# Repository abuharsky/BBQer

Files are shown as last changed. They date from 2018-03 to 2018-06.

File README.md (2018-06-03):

> This is the first, alpha version of documentation. It will be improved. I'll waiting for your questions

# BBQer
Hello, my name is Alex, I'm from Russia and I love BBQ!
So, BBQ Smokers are not so popular in Russia, thats why I'am the only one in my small town - therefore the best :) !

There are a lot of different handmade of factorymade BBQ Smoker temperature controllers, but for me all of them have too many limitations.
For example, for assembling very popular "HeaterMeter" you need to be an good engineer with soldering skills.
Or, you need to spent a lot of time to assemble, debug and configure some other DIY projects.
Or it cost too much!

As for me, this is not an easy way.

I hope, that I can explain to you, how to get very easy, cheap, really, extra-cheap controller with an optional cloud monitoring, that perfectly solve every BBQSmoking needs!

### Let's begin!

What's is the main problem for Low&Slow smoking?! Right, it takes too many hours! You need to constantly maintain temperature level and smoke density.

For maintaining constant temperature you need to always change an airflow using damper.

Airflow provide the main heat and smoke transfer from burning wood and charcoals to the meat.

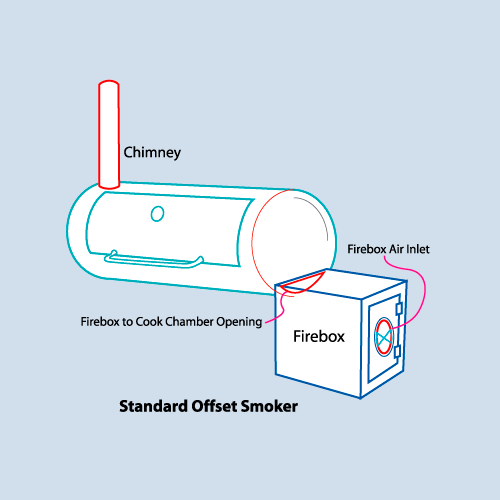
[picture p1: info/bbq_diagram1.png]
standart offset smoker


So, we need only to add a simple temperature sensor and electronically controlled air blower/damper.
Controller periodically reads temperature and adjust the airflow.

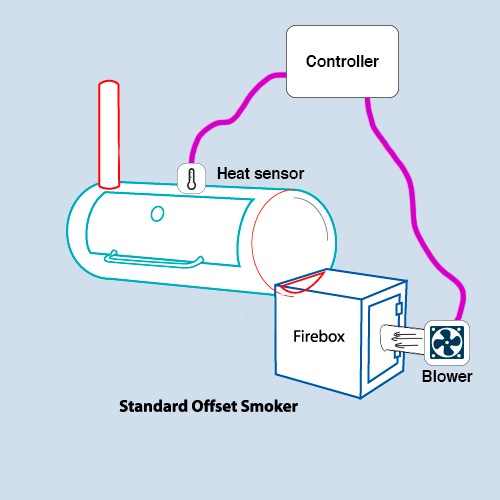
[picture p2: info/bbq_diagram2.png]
standart offset smoker with temperature controller


That's how does it must work.

### Part 1. Arduino based controller

### Hardware

As I say before, I don't think that we need to be an engineer with soldering skills! You don't need to solder anything (maybe exept few connectors).

You need to buy:

1x [arduino nano (~3$)](https://ru.aliexpress.com/store/product/Arduino-Nano-3-0-Arduino-Nano-CH340-usb/1602024_32841140539.html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)

1x [arduino nano I/O extension board(~1$)](https://ru.aliexpress.com/item/1Pcs-I2C-NANO-I-O-Expansion-Sensor-Shield-Module-For-Arduino-UNO-R3-Nano-V3-0/32829846130.html)

1x [temperature sensor (K-type thermocouple with required amplifier)(~3$)](https://ru.aliexpress.com/item/MAX6675-Module-K-Type-Thermocouple-Temperature-Sensor/32698965438.html)

1x [blower fan(~2.5$)](https://ru.aliexpress.com/item/Brushless-DC-Blower-Cooling-Fan-Sleeve-Bearing-7525S-12V-0-18A-75x33mm-75mm/32731387269.html)

1x [mosfet driver(~0.5$)](https://ru.aliexpress.com/item/TOP-MOSFET-Button-IRF520-MOSFET-Driver-Module-ARM-Raspberry-pi/32662485350.html)

1x [wires (~3$)](https://ru.aliexpress.com/item/Dupont-Wire-Male-to-Male-Male-to-Female-Female-to-Female-Jumper-Cable-120x10cm/32729974130.html)

1x [power converter (~1$)](https://ru.aliexpress.com/item/XL6009-DC-Adjustable-Step-up-boost-Power-Converter-Module-Replace-LM2577/32636472543.html)

##### Total: ~14$ (without delivery)
(I recommend to use same supplier for faster delivery)

Also, you can optionally purchase:

1x [servo (~3$)](https://ru.aliexpress.com/item/MG90S-Micro-Servo-RC/32843925047.html?spm=a2g0s.9042311.0.0.jh7MDU) for more fine aiflow control

1x [thermo probe (~7$)](https://ru.aliexpress.com/item/Thermopro-Thermometer-extra-probe/32778050836.html?spm=a2g0s.9042311.0.0.jh7MDU) for food(meat) temperature control. You can connect up to 8 probes.

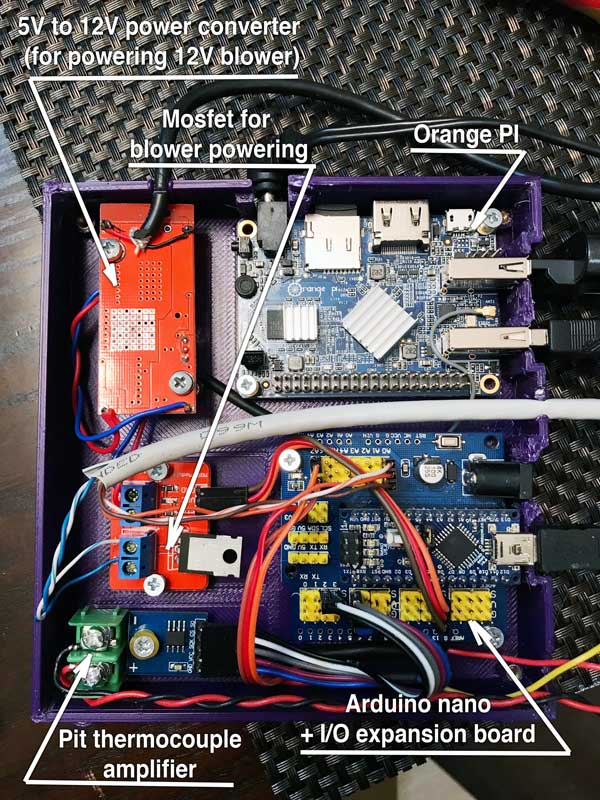
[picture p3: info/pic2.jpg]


# BEFORE ASSEMBLING!!!

Don't connect your motor to power converter.
First you need to adjust output voltage to 12V.
Using multimeter adjust voltage regulator on the blue box.

### Software

first, you need to add to your arduino *[SerialCommand](https://github.com/kroimon/Arduino-SerialCommand)* library

next, flash an arduino using this **repository/arduino/BBQController/**

next, open serial monitor (baud 115200) and type any of commands below:

* **target** <temp> - set target temp to specified value, this command start temperature controller, example: "target 110" - set the target temp to 110С or "target 0" - disables temperature controller

optional, manual managment commands:

* **temp** - print current temp from all sensors
* **servo** <angle> - move servo to specified angle
* **damper** <position> - open or close damper, position value between 0.0(closed) and 1.0(fully opened)
* **motor** <power> - powers the blower, power value between 0.0(disabled) and 1.0(full power)

This is enougth! You can setup your arduino controller, all values will be stored in EEPROM(energy independent memory). So, set the target temp to 110C (for brisket) and use great and cheap temperature controller.

I think, that we don't need to setup an additional display for arduino controller (Maybe I'll change my opinion in the future).
If you need display or some kind of user interface to this arduino controller, let's go to part 2!

### Part 2. Orange PI + cloud monitoring

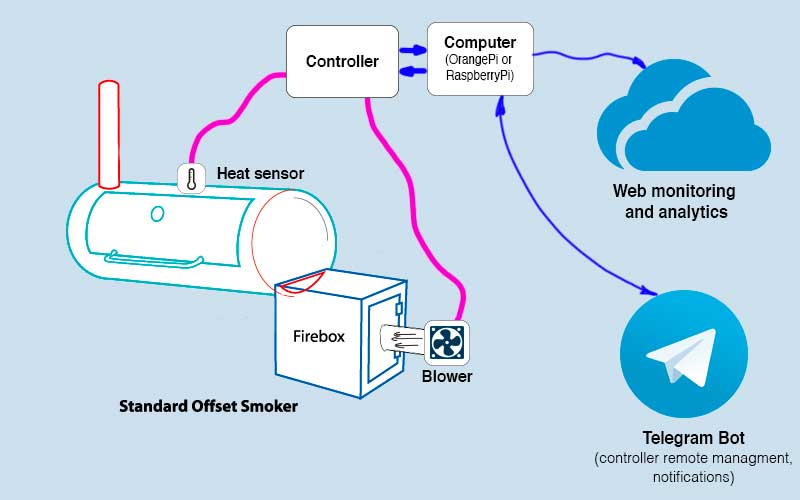
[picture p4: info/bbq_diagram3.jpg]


### Hardware

I recommend to use an orange pi lite (~12$).

### Software

As I say before, I don't want to setup direct display with some buttons on arduino. Because everyone already have display!
We will use your phones and tablets! And, of course, internet!

So, after you setup your PI (you can use one of thousands instructions from internet), you need to setup python3 and required packages, just type in the pi terminal the commands below:

> apt-get install python3
> 
> apt-get install python3-pip
> 
> pip3 install requests
> 
> pip3 install telebot
> 
> pip3 install pyserial

After installing, copy 
BBQer/cloudClient/bbqcontroller.py

BBQer/cloudClient/configuration_empty.txt

to your pi home dir, then, **rename configuration_empty.txt** to **configuration.txt** and fill required parameters

We will use telegram bot for sending commands to controller and receive information.

### Cloud monitoring

I recommend to use **corlysis.com** , free account is enough for our temperature monitoring.

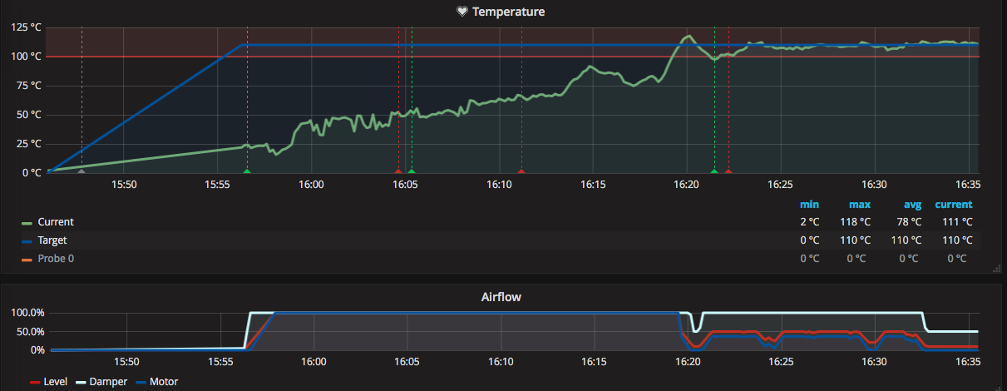
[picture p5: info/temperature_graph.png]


Setup database, than copy required db name and token to **configuration.txt**, than open grafana and import dashboard from **grafana.json**

Now, you can use your mobile phone to control your BBQ, view temperature graphs and receive notifications!

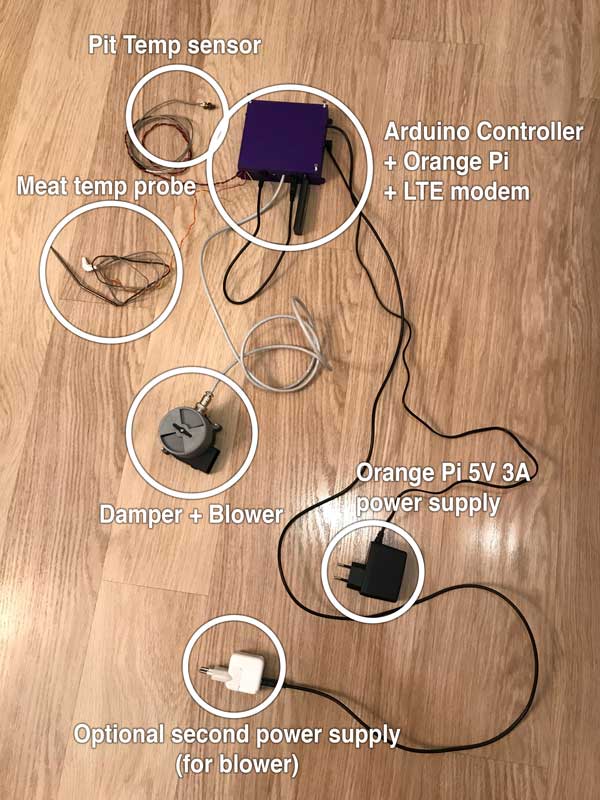
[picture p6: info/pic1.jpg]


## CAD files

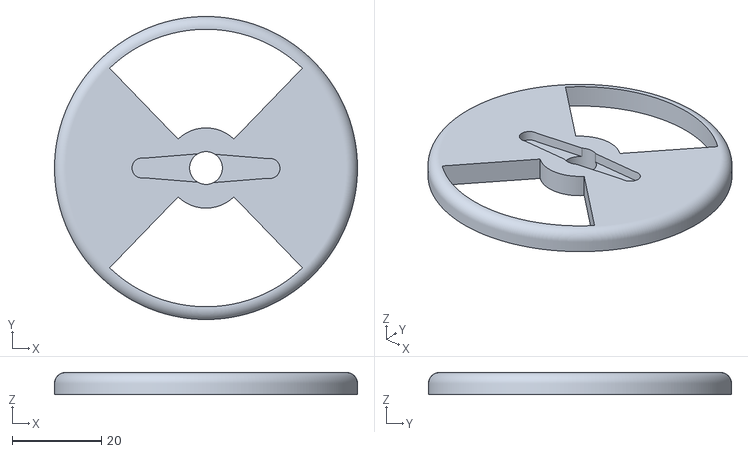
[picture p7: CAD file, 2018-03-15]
3dprint/damper_top.stl
68.0 x 68.0 x 5.00

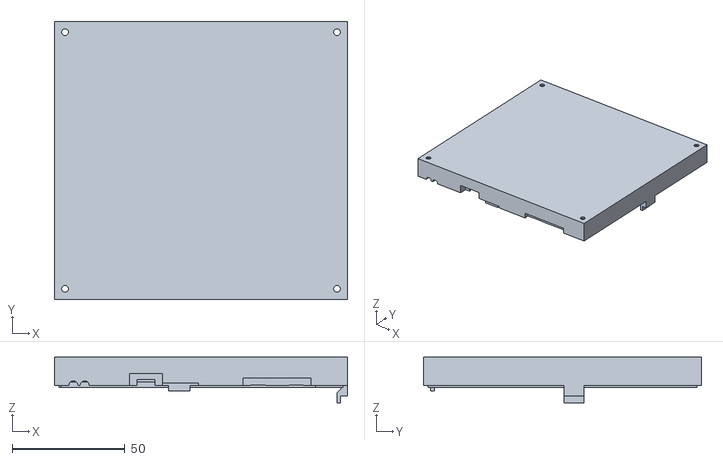
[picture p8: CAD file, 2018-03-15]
3dprint/electronics_box_top.stl
130.0 x 123.2 x 20.2

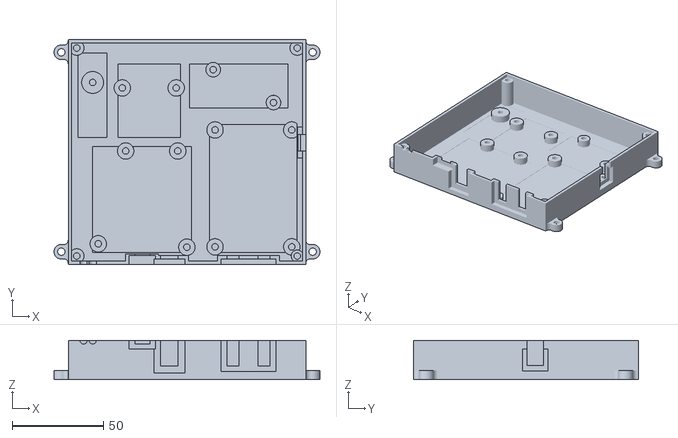
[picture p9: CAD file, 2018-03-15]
3dprint/electronics_box_bottom.stl
145.6 x 123.2 x 21.5

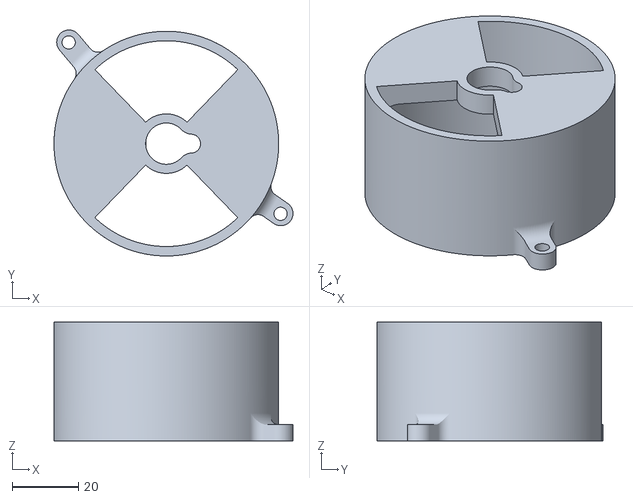
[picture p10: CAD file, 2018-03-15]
3dprint/damper_bottom.stl
72.3 x 68.4 x 36.0

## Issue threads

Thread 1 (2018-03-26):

Schematic needed

TorokBalazs75, 2018-03-26:
hello abuharsky, I love BBQing just like you probably, so I was glad reading your comment on arduino project hub, but honestly I'm a real beginner building a controller like this. Is it possible to have a schematic  for the electronics? Next will be the programming, but I hope I will help with that one :) thanks a lot, Balázs

abuharsky, 2018-03-27:
Ok, no problem I will add schematic very very soon

TorokBalazs75, 2018-03-27:
👍

TorokBalazs75, 2018-04-25:
hi there, schematic is more professional, but even if you could pull apart the boards little bit to see the wiring better would be helpful, thanks&regards, Balázs

abuharsky, 2018-05-23:
Im sorry for long answer, I tried some schematic tools, but they dont have a lot of used components, so, I can make a video

TorokBalazs75, 2018-05-23:
actually - as I'm still learning - found that it is pretty much well defined in the source code, but a video might be helpful

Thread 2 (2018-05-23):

max6675 error

TorokBalazs75, 2018-05-23:
hi Abuharsky, finaly I got my parts and started to work on the project, but unfortunately ran into an issue already. When I try to upload the controlling program to arduino, it fails with missing source-code for max6675, could you please advise? thanks a lot

abuharsky, 2018-05-23:
ooh, no problem, just download this one

https://github.com/adafruit/MAX6675-library

and put it to your arduino library folder or use this instruction

https://www.arduino.cc/en/Guide/Libraries#toc5

abuharsky, 2018-05-23:
no problem

TorokBalazs75, 2018-05-23:
hi, so I successfully loaded code on arduino, connected everything together. Now I can communicate with arduino, thermocouple reads temp. However damper open/closes on command, if current temp is 23 and I set target to 30, I would expect damper close and ventillator turn off when reaching target temp, but it doesn't happen so:

[BBQctrler_1st_use.txt](https://github.com/abuharsky/BBQer/files/2032538/BBQctrler_1st_use.txt)

also, at first, I used a 5V blower attached to the mosfet, then I wanted to try the 12V blower through the booster  connected to mosfet, but only gave clicking noise, then I put back the 5V blower to mosfet, but it doesn't work, so I'm afraid, that something happend to the mosfet :(

abuharsky, 2018-05-23:
make a photo of assembled electronics

TorokBalazs75, 2018-05-23:
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

abuharsky, 2018-05-23:
contact me on fb https://www.facebook.com/abuharsky

jzGitHub-01, 2020-01-13:
Hi abuharsky,
Can I ask you some question which realted to bbq topic?
Maybe on FB?

MTBrewer, 2020-06-17:
Did you ever figure out your damper and what was causing the clicking noise in the blower?

abuharsky, 2020-06-20:
Noise is ok, you hear it because of PWM signal.

stunt77, 2020-08-04:
Hi, same problem blower stopped with noise, how i can solve tks

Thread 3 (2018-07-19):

Grill Open Logic

paintflinger, 2018-07-19:
Trying to teach myself the programming language to potentially incorporate myself, but have you considered adding programming logic for when you open up the grill?

For example, if the Grill Temperature decreases at a rate greater than 2 degrees / second then the temperature controller will exit the control loop for a set period (e.g. 5 minutes) to allow the grill to achieve steady state again.

abuharsky, 2018-07-23:
Maybe Grill Door open/close sensor needed. I will make some experiments.

Thank you for idea.

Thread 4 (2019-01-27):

Schematic

ghojezz, 2019-01-27:
Hello there,

I'm really new to this kind of thing and I don't have any background in tinkering with electronics, arduino, etc but I'm willing to learn. Can you draw us a diagram using Fritzing application if you don't mind?

abuharsky, 2019-01-27:
Hey!

I working for a new version, that twice as cheaper and twice as easier to assemble. But with the same level of functionality!

I dont want to work more about this old version, so, I will describe deeply new version to help ypu to assemble it.

I you want, I can say you part numbers of new components.
While you will wait for delivery, I will make some new wiki articles.

mhnudi, 2019-07-16:
Hello! I was just reading through some of your comments and found this one saying you might be working on a newer version. I was just wondering if this was still the case? I am hoping to perform a similar modification like you have but if you are in the process of working on a simpler version I would definitely be interested. Thanks!

alambert-irl, 2020-04-20:
Hi @abuharsky.

Alex here, just been looking at building your project. I can see from your photos that you have a damper and fan combined. Do you have a link for the damper you used, are you using this [servo](https://aliexpress.ru/item/32843925047.html?spm=a2g0s.9042311.0.0.jh7MDU)to control the damper?

Thanks - Alex trying to survive quarantine in Ireland

abuharsky, 2020-04-29:
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

Hi, sorry for late answer, yea, servo is ok

jlsegb, 2020-06-26:
In case anyone is struggling like my friends and I were. Here are more pictures with a little more detail.
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

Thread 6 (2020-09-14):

Cloud / Telegram issue?

balazsraacz, 2020-09-14:
Hi Alexander,

not sure if this project is still open or used by anyone. Despite all my efforts I can't get the communication with telegram working and getting errors with the python file as well.

 "python3 bbqcontroller.py"
I get the following error:
"root@orangepilite:~/BBQer/cloudClient# python3 bbqcontroller.py
Traceback (most recent call last):
  File "bbqcontroller.py", line 10, in <module>
    config.read('/root/BBQer/cloudClient/configuration.txt')
  File "/usr/lib/python3.5/configparser.py", line 696, in read
    self._read(fp, filename)
  File "/usr/lib/python3.5/configparser.py", line 1077, in _read
    raise MissingSectionHeaderError(fpname, lineno, line)
configparser.MissingSectionHeaderError: File contains no section headers.
file: '/root/BBQer/cloudClient/configuration.txt', line: 1
'\ufeff[arduino]\n'
"

Either way appreciate the help

balazsraacz, 2020-10-18:
The solution to run the script seems to have been the config file it pulled in was in the root rather than the correct in home.

Closed 2020-10-18.

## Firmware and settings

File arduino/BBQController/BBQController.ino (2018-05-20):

#include <SerialCommand.h>
#include "max6675.h"
#include <Servo.h>
#include "DCMotor.h"
#include "SmoothServo.h"
#include "Damper.h"
#include "ThermoProbe.h"
#include "TemperatureController.h"

#define SERVO_PIN A0
#define SERVO_MIN_ANGLE 0
#define SERVO_MAX_ANGLE 90

#define MOTOR_PIN 11

#define PROBE0_PIN A4
#define PROBE1_PIN A7

#define THERMO_S0  2
#define THERMO_CS  3
#define THERMO_CLK 4


Servo servo;
SmoothServo smoothServo(servo, SERVO_PIN);
DCMotor motor(MOTOR_PIN);
Damper damper(smoothServo, SERVO_MIN_ANGLE, SERVO_MAX_ANGLE);
MAX6675 thermocouple(THERMO_CLK, THERMO_CS, THERMO_S0);
ThermoProbe probe0(PROBE0_PIN, 200000, 4220);
ThermoProbe probe1(PROBE1_PIN, 200000, 4220);

TemperatureController controller(damper, motor, thermocouple, probe0, probe1);

SerialCommand sCmd;

void setup()
{
  Serial.begin(115200);

  motor.setup();
  controller.setup();
  probe0.setup();
  probe1.setup();

  // Setup callbacks for SerialCommand commands
  sCmd.addCommand("servo", servoControl);
  sCmd.addCommand("damper", damperControl);
  sCmd.addCommand("motor", motorControl);
  sCmd.addCommand("temp", getTemperature);
  sCmd.addCommand("target", setTargetTemperature);
  sCmd.addCommand("controller", setControllerParameters);
  sCmd.setDefaultHandler(unrecognized);

  Serial.println("Ready");
}

void loop()
{
  motor.loop();
  controller.loop();
  probe0.loop();
  probe1.loop();
  sCmd.readSerial();
}

//---------------------------------------------

void servoControl() {
  char *arg;

  arg = sCmd.next();
  if (arg != NULL) {
    smoothServo.setAngle(atoi(arg)); 
    smoothServo.printState();
  }


}

void damperControl() {
  char *arg;

  arg = sCmd.next();
  if (arg != NULL) {
    damper.setPosition(atof(arg)); 
    damper.printState();
 }


}

void motorControl() {
  char *arg;

  arg = sCmd.next();
  if (arg != NULL) {
    motor.setPower(atof(arg));
    motor.printState();
  }

}

void setTargetTemperature() {
  char *arg;

  arg = sCmd.next();
  if (arg != NULL) {
    controller.setTargetTemperature(atof(arg));
  }

  arg = sCmd.next();
  if (arg != NULL) {
    controller.setPrintStateInterval(atof(arg)*1000);
  }
}

void setControllerParameters() {
  char *printInterval   = sCmd.next();
  char *airFlowMin      = sCmd.next();
  char *airFlowMax      = sCmd.next();
  char *airFlowStepUp   = sCmd.next();
  char *airFlowStepDown = sCmd.next();
  
  if (printInterval != NULL && 
      airFlowMin != NULL && airFlowMax != NULL && 
      airFlowStepUp != NULL && airFlowStepDown != NULL) 
  {
    controller.setPrintStateInterval(atof(printInterval)*1000);
    controller.setAirflowLimitsAfterTempReached(atof(airFlowMin), atof(airFlowMax));
    controller.setAirflowChangeSteps(atof(airFlowStepUp), atof(airFlowStepDown));

    controller.printParameters();
  }
  else {
    Serial.println("Wrong 'controller' command arguments, must be:");
    Serial.println("> controller printInterval(seconds) airFlowMinWhenTempReached(float) airFlowMaxWhenTempReached(float) airFlowStepUp(float) airFlowStepDown(float)");
    Serial.println("Example:");
    Serial.println("> controller 10 0.3 0.7 0.05 0.15");
  }

}

void getTemperature() {
  Serial.print("[TEMP] PIT=");
  Serial.print(thermocouple.readCelsius());
  Serial.print("C, PROBE1=");
  Serial.print(probe0.readCelsius());
  Serial.print("C, PROBE2=");
  Serial.print(probe1.readCelsius());
  Serial.print("C");
  Serial.println();
}

void unrecognized(const char *command) {
  Serial.println("Unrecognized command");
}

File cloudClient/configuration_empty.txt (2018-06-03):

[arduino]
port=/dev/ttyUSB0
baud=115200

[telegram]
chatId=111222
botToken=511122334455:XXXXXXXXX-XXXXXXXXX-XXXXXXXXX
proxyType=
proxyAddress=

[corlysis]
db=BBQControl
token=XXXXXXXXXXXXXXXXXXXXXXXXXXX

[system]
runCommandOnNoInternet=sudo ifconfig wlan0 down && sleep 5 && sudo ifconfig wlan0 up && exit 0

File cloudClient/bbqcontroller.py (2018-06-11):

#!/usr/bin/python
import serial, time, threading, json, datetime, requests, configparser, os, queue, logging
#-------------------------
# config
#-------------------------

config = configparser.ConfigParser()
config.read('/root/BBQer/cloudClient/configuration.txt')

usbDevice = config.get('arduino', 'port')
usbSpeed  = config.get('arduino', 'baud')

chatId       = config.get('telegram', 'chatId')
botToken     = config.get('telegram', 'botToken')
proxyType    = config.get('telegram', 'proxyType')
proxyAddress = config.get('telegram', 'proxyAddress')

proxy = {}
if proxyType and proxyAddress:
	proxy = {proxyType:proxyAddress}

dbName    = config.get('corlysis', 'db')
dbToken   = config.get('corlysis', 'token')

networkLostCommand = config.get('system', 'runCommandOnNoInternet')
networkRestartRetriesBeforeRestart = 0
networkRestartMaxRetries = 5
networkErrorsCounter = 0 #count every send operation error
networkMaxErrorCount = 5

#---------
serial_port = serial.Serial(usbDevice, usbSpeed)

main_thread_queue = queue.Queue()
network_thread_queue = queue.Queue()

logging.basicConfig(filename="/root/BBQer/cloudClient/logs/bbqcontroller"+str(time.time())+".log", level=logging.INFO)


def run_on_main_thread(function):
	main_thread_queue.put(function)

def run_on_network_thread(function):
	network_thread_queue.put(function)

#-------------------------
# corlysis
#-------------------------

def plot_json(data):
	obj = json.loads(data)

	# currenttime = '{0:%H:%M:%S}'.format(datetime.datetime.now())

	airflow  = obj["airflow"]["level"]
	damper   = obj["airflow"]["damper"]
	motor    = obj["airflow"]["motor"]
	curtemp  = obj["temperature"]["current"]
	probe0   = obj["temperature"]["probe0"]
	probe1   = obj["temperature"]["probe1"]
	target   = obj["temperature"]["target"]

	url = 'https://corlysis.com:8086/write'
	
	params = {"db": dbName, "u": "token", "p": dbToken}
	
	payload = "temperature_data current="+curtemp+",target="+target+",probe0="+probe0+",probe1="+probe1+"\nairflow_data level="+airflow+",damper="+damper+",motor="+motor+"\n"
	
	global networkErrorsCounter
	try:
		resp = requests.post(url, params=params, data=payload, timeout=10)
		resp.raise_for_status()
	except Exception as err:
		networkErrorsCounter += 1
		logging.info('Error sending plot data: ' + str(err))
		print('Error sending plot data: ' + str(err) + '\n' + payload)


#-------------------------
# serial
#-------------------------

def write_line_to_serial_port(line):
	logging.info('[serial] <- ' + line)
	print('[serial] <- ' + line)
	serial_port.write(line.encode())
	serial_port.write(b'\n')

def handle_serial_port_data(data):
	logging.info('[serial] -> ' + data)
	print('[serial] -> ' + data)
	
	# detect json data
	if (data.startswith( '{' )):
		run_on_network_thread(lambda: plot_json(data))
	else:
		run_on_network_thread(lambda: telegram_send_message(chatId, 'serial: '+data))

def read_from_serial_port(serial_port):
	while True:
		line = serial_port.readline().decode()
		run_on_main_thread(lambda: handle_serial_port_data(line))
		time.sleep(1)

thread_serial_port = threading.Thread(target=read_from_serial_port, args=(serial_port,))
thread_serial_port.start()


#-------------------------
# telegram bot
#-------------------------

def telegram_send_message(to, text):
	global networkErrorsCounter
	try:
		resp = requests.get('https://api.telegram.org/bot' + botToken + '/sendMessage?chat_id=' + to + '&text=' + text, proxies=proxy, timeout=10)
		resp.raise_for_status()
	except Exception as err:
		networkErrorsCounter += 1
		logging.info('Error sending message to telegram ' + str(err))
		print('Error sending message to telegram ' + str(err))

def telegram_get_updates():
	offset = 0
	while True:
		try:
			resp = requests.get('https://api.telegram.org/bot' + botToken + '/getUpdates?timeout=30&allowed_updates=["message"]&offset=' + str(offset), proxies=proxy, timeout=30)
			if resp.status_code == 200:
				offset = process_telegram_updates_response(resp.json())
			else:
				resp.raise_for_status()
		except requests.exceptions.Timeout:
			time.sleep(3) #no updates, run next iteration
			continue
		except Exception as err:
			logging.info('telegram "getUpdates" error: ' + str(err))
			print('telegram "getUpdates" error: ' + str(err))
			time.sleep(15)
			continue
		time.sleep(1)

def process_telegram_updates_response(json):
	offset = 0
	updates = json["result"]
	for index, update in enumerate(updates):
		run_on_main_thread(lambda: process_telegram_message(update["message"]))
		offset = int(update["update_id"])
	return offset + 1

def process_telegram_message(message_json):
	if chatId == str(message_json["from"]["id"]): 
		text = message_json["text"]
		logging.info('[telegram] ' + text)
		print('[telegram] ' + text)
		if text.startswith('/cputemp'):
			file = open("/etc/armbianmonitor/datasources/soctemp", "r")
			run_on_network_thread(lambda: telegram_send_message(chatId, "CPU temp:{:.1f}C".format(float(file.read())/1000)))  
		elif text.startswith('/serial'):
			run_on_main_thread(lambda: write_line_to_serial_port(text[8:]))
		elif text.startswith('/shutdown'):
			run_on_network_thread(lambda: telegram_send_message(chatId, "Shutting down..."))  
			run_on_main_thread(lambda: os.system('systemctl poweroff'))

thread_telegram_bot = threading.Thread(target=telegram_get_updates)
thread_telegram_bot.start()


#-------------------------
# internet connection 
# checker
#-------------------------

def connected_to_internet():
	global networkErrorsCounter
	if networkErrorsCounter > networkMaxErrorCount:
		print("Too many network errors")
		networkErrorsCounter = 0
		return False
	
	try:
		response = requests.get('https://api.telegram.org/bot' + botToken + '/getMe', proxies=proxy, timeout=10)
		response.raise_for_status()
		return True
	except Exception as e:
		logging.info("No internet connection available. " + str(e))
		print("No internet connection available. " + str(e))
	return False

def check_internet_connection_and_reconnect():
	while True:
		print('checking internet')
		if not connected_to_internet():
			global networkRestartRetriesBeforeRestart
			if (networkRestartRetriesBeforeRestart < networkRestartMaxRetries):
				logging.info('no internet, running command')
				print('no internet, running command')
				networkRestartRetriesBeforeRestart += 1
				os.system(networkLostCommand)
				run_on_network_thread(lambda: telegram_send_message(chatId, 'reconnected to the internet.'))
			else:
				logging.info('no internet, rebooting')
				print('no internet, rebooting')
				os.system('reboot')
		else:
			networkRestartRetriesBeforeRestart = 0
			print('internet OK')
		time.sleep(60)


thread_check_internet = threading.Thread(target=check_internet_connection_and_reconnect)
thread_check_internet.start()

#-------------------------
# main loop and  
# threaded task processing
#-------------------------
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

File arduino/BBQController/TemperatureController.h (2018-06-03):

#ifndef TemperatureController_h
#define TemperatureController_h

#include <EEPROM.h>
#include "DCMotor.h"
#include "SmoothServo.h"
#include "Damper.h"
#include "ThermoProbe.h"

class TemperatureController {
    Damper &damper;
    ThermoProbe &probe0;
    ThermoProbe &probe1;
    DCMotor &motor;
    MAX6675 &thermocouple;

    float targetTemperature = 0.00f;

    unsigned long lastPrintStateMs = 0;
    unsigned long printStateInterval = 10000;

    unsigned long lastMs = 0;

    unsigned long stepMs = 1 * 1000; // 1 sec
    
    float airFlowLevel = 0.0;

    float minAirFlowLevelAfterTempReached = 0.0; // decrease airflow limits when 
    float maxAirFlowLevelAfterTempReached = 1.0; // temperature has reached target first time
    boolean isTemperatureReachedFirstTime = false;

    float airFlowUpStep   = 0.05; // percent
    float airFlowDownStep = 0.05; // percent

  public:
    TemperatureController(Damper &damper, DCMotor &motor, MAX6675 &thermocouple, ThermoProbe &probe0, ThermoProbe &probe1) :
      damper(damper), motor(motor), thermocouple(thermocouple), probe0(probe0), probe1(probe1) {
    }

    void setup() {
      
      EEPROM.get(0, targetTemperature); 
      if (targetTemperature < 0 || targetTemperature > 300) {
        setTargetTemperature(0);
      }

      EEPROM.get(sizeof(float), printStateInterval); 
      if (printStateInterval < 3000) { // min 3 sec
        setPrintStateInterval(3000);
      }

      EEPROM.get(sizeof(float)*2, minAirFlowLevelAfterTempReached); 
      if (minAirFlowLevelAfterTempReached < 0.0 || minAirFlowLevelAfterTempReached > 1.0) {
        minAirFlowLevelAfterTempReached = 0.0;
      }

      EEPROM.get(sizeof(float)*3, maxAirFlowLevelAfterTempReached); 
      if (maxAirFlowLevelAfterTempReached > 1.0 || maxAirFlowLevelAfterTempReached < 0.0) {
        maxAirFlowLevelAfterTempReached = 1.0;
      }

      EEPROM.get(sizeof(float)*4, airFlowUpStep); 
      if (airFlowUpStep <= 0.0 || airFlowUpStep > 1.0) {
        airFlowUpStep = 0.05;
      }

      EEPROM.get(sizeof(float)*5, airFlowDownStep); 
      if (airFlowDownStep <= 0 || airFlowDownStep > 1.0) {
        airFlowDownStep = 0.05;
      }
    }

    void loop() {

      if (targetTemperature != 0.0) {
          unsigned long ms = millis();
          if (ms - lastMs > stepMs) {
            lastMs = ms;
    
            float temp = thermocouple.readCelsius();
    
            if (temp < targetTemperature) {
              setAirFlowLevel(airFlowLevel + airFlowUpStep);
            }
            else {
              isTemperatureReachedFirstTime = true;
              setAirFlowLevel(airFlowLevel - airFlowDownStep);
            }
          }

          printCurrentStateIfNeeded();
      }
    }

    
    void setAirFlowLevel(float level) {

      float minAirFlowLevel = 0.0;
      float maxAirFlowLevel = 1.0;

      if (isTemperatureReachedFirstTime) {
        minAirFlowLevel = minAirFlowLevelAfterTempReached;
        maxAirFlowLevel = maxAirFlowLevelAfterTempReached;
      }

      
      if (level > maxAirFlowLevel) {
        level = maxAirFlowLevel;
      }
      
      if (level < minAirFlowLevel) {
        level = minAirFlowLevel;
      }

      airFlowLevel = level;
            
      float maxDamperPercent = 0.2;
      if (level <= maxDamperPercent) {
        damper.setPosition(level/maxDamperPercent);
        motor.setPower(0);
      }
      else {
        damper.setPosition(1);
        float power = (level - maxDamperPercent) / (1.0 - maxDamperPercent);
        motor.setPower(power);
      }
    }
    
    void setTargetTemperature(float targetTemp) {
      isTemperatureReachedFirstTime = false;
      
      targetTemperature = targetTemp;
      EEPROM.put(0, targetTemperature); 

      if (targetTemperature == 0) {

        setAirFlowLevel(0);
        
        Serial.println("[CONTROLLER] off");
        printCurrentState();

        return;
      }

    }

    void setAirflowLimitsAfterTempReached(float minAirFlow, float maxAirFlow) {
      minAirFlowLevelAfterTempReached = minAirFlow;
      EEPROM.put(sizeof(float)*2, minAirFlowLevelAfterTempReached); 

      maxAirFlowLevelAfterTempReached = maxAirFlow;
      EEPROM.put(sizeof(float)*3, maxAirFlowLevelAfterTempReached); 
    }

    void setAirflowChangeSteps(float stepUp, float stepDown) {
      airFlowUpStep = stepUp;
      EEPROM.put(sizeof(float)*4, airFlowUpStep); 

      airFlowDownStep = stepDown;
      EEPROM.put(sizeof(float)*5, airFlowDownStep); 
    }

    void setPrintStateInterval(float interval) {
      printStateInterval = interval;
      EEPROM.put(sizeof(float), printStateInterval); 
    }
  
    void printCurrentStateIfNeeded() {      
      if (millis() - lastPrintStateMs > printStateInterval) {
        lastPrintStateMs = millis();
        printCurrentState();
      }
    }

    void printParameters() {
        Serial.println("[CONTROLLER]");
        Serial.print("> printInterval(seconds) = "); 
          Serial.println(printStateInterval/1000);
        Serial.print("> airflow(when target temp reached): min = "); 
          Serial.print(minAirFlowLevelAfterTempReached);
          Serial.print(", max = "); 
          Serial.println(maxAirFlowLevelAfterTempReached);
        Serial.print("> airflow step: up = "); 
          Serial.print(airFlowUpStep);
          Serial.print(", down = "); 
          Serial.println(airFlowDownStep);
    }

    void printCurrentState() {
      
      float pitTemp = thermocouple.readCelsius();
      if (isnan(pitTemp)) {
        pitTemp = 0;
      }
      
      Serial.print("{");
          Serial.print("\"airflow\": {");
              Serial.print("\"level\": \"");    Serial.print(airFlowLevel);               Serial.print("\",");
              Serial.print("\"damper\": \"");   Serial.print(damper.getPosition());       Serial.print("\",");
              Serial.print("\"motor\": \"");    Serial.print(motor.getPower());           Serial.print("\"");
          Serial.print("},");
          Serial.print("\"temperature\": {");
              Serial.print("\"current\": \"");  Serial.print(pitTemp);                    Serial.print("\",");
              Serial.print("\"probe0\": \"");   Serial.print(probe0.readCelsius());       Serial.print("\",");
              Serial.print("\"probe1\": \"");   Serial.print(probe1.readCelsius());       Serial.print("\",");
              Serial.print("\"target\": \"");   Serial.print(targetTemperature);          Serial.print("\"");
          Serial.print("}");
      Serial.print("}");

      Serial.println();
    }
};

#endif

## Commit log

2018-03-15 updated project structure, added sample config file
    [configuration_empty.txt, damper_bottom.stl, damper_top.stl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]
2018-04-15 added 2nd probe
2018-04-21 added 2nd probe, added proxy support
    [configuration_empty.txt]
2018-05-20 thermistor calibrating
2018-05-20 thermistor test
2018-05-20 thermistor test done
2018-06-03 Improved core functionality. Added network reachability watchdog + ability to run shell command on lost network connection
    [configuration_empty.txt]
